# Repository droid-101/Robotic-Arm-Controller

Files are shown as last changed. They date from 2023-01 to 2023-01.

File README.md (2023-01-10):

# Robotic Arm Controller

## Background

### Pulse Width Modulation (PWM)

Pule Width Modulation is a a technique of sending variable electrical signals by using digital pulses. By turning a digital output on and off at varying frequencies, an effect can be produced where the signal is recieved at a fraction of the power. For example, a digital signal which is switched between an on state and an off state in equal intervals (50% of the time) will appear to be on at half power. Using this technique of altering the frequencies of these square pulses which are digital signals, variable electrical signals can be created using digital outputs. The servo motors on the robotic arm utilize PWM signals to operate. The PWM wires consist of three different wires carrying 5V+, signal, and GND respectively.

## Robotic Arm

The robotic arm has four different degrees of freedom, each controlled by a small servo motor. These four motors control rotation on the base, extension of the arm, the height of the claws, and the opening and closing of the claws. Each servo motor has a PWM cable over which it can recieve signals from the controller.

Robotic Arm

## Controller

The controller is a custom made Printed Circuit Board (PCB) which interfaces with the robotic arm's servo motors. It is designed to be plugged into a breadboard and connect to both an external microprocessor, and the robotic arm.

### Power Supply

The controller recieves power through a barrel jack. A 9V adapter is used to plug into a 120V wall socket and supplies the board with power through the barrel jack. Most of the electronic components on the board, as well as the servo motors on the arm, run on 5V. To downstep the voltage, three 7805 voltage regulators are used in parallel to both supply 5V to the circuit, and to prevent the board from overheating from high current draw.

### Controls

The controller has four potentiometers and one button as a part of its control set. Each potentiometer is isolated on its own channel on which it can be sampled for its current value by an external microprocessor. This allows for each joint on the robotic arm to have its own separate control. The button on the circuit board can also be read for its current state. It can serve as a trigger, or as a reset button.

### Reading and Writing

The controller has multiple sets of sip pins which connect to different components. The row of five sip pins connect to the button and potentionmeters and serve as inputs for the microprocessor to sample. The row of four sip pins are output pins which the microprocessor can use to write PWM signals to the servo motors. Each pin corresponds to a specific servo motor on the arm. The last set of four rows of three sip pins are connectors for the servo motors and allow for each motor to recieve power, and its respective signal from the microprocessor.

### Schematic
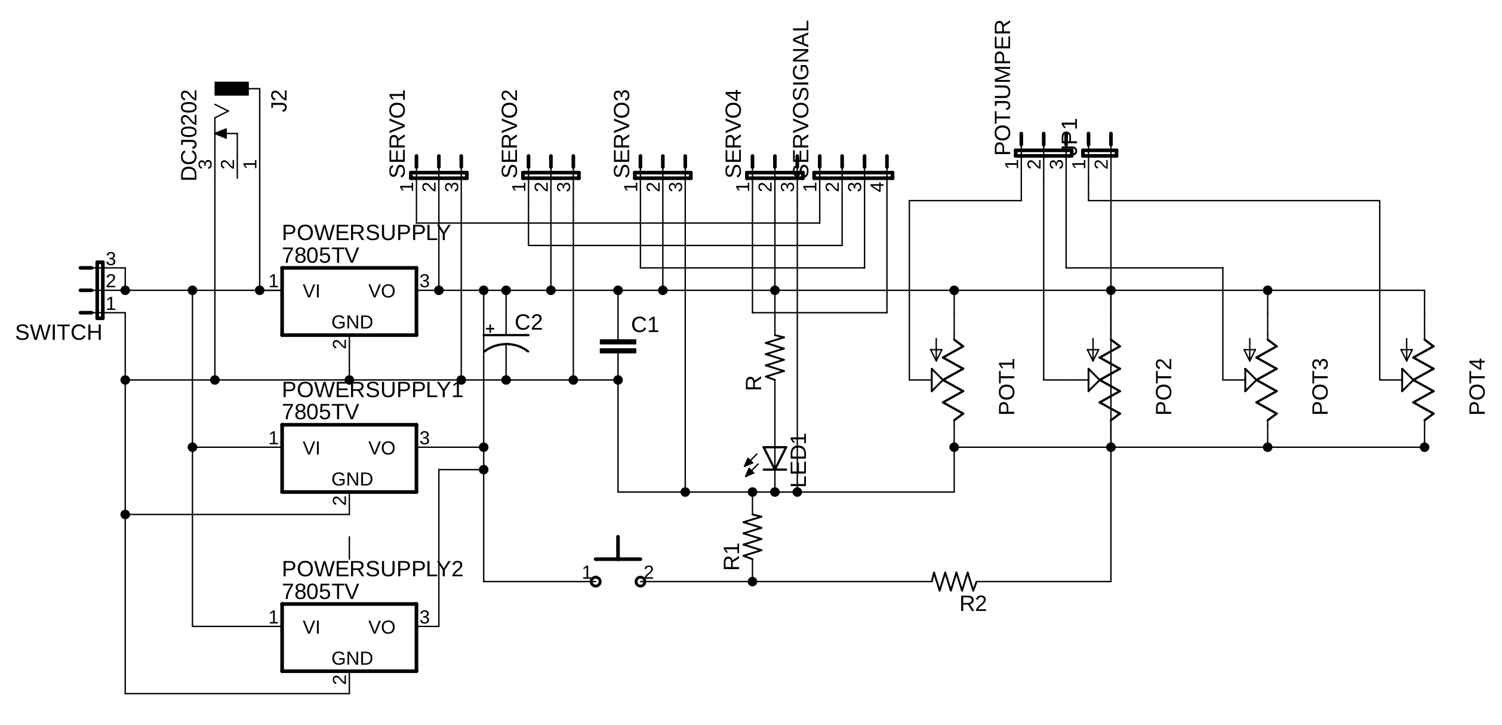
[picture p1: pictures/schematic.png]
Schematic


### Trace Mask
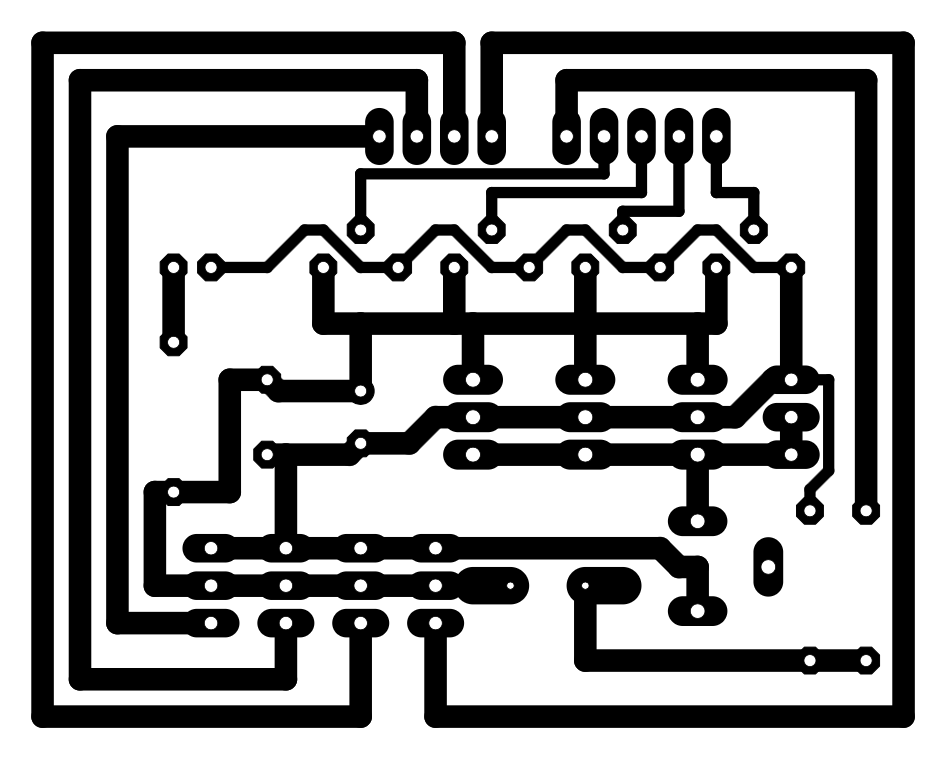
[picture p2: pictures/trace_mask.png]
Trace Mask


### Controller Circuit Board
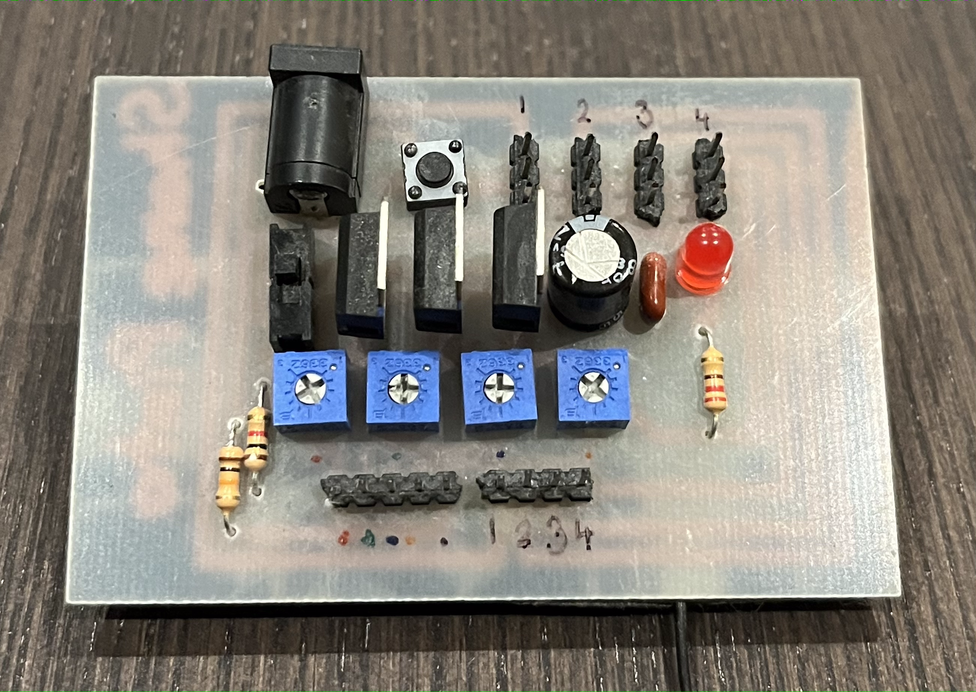
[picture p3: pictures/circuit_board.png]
Controller Circuit Board


## Arduino

The controller board was connected to an Arduino to manage reading the controls and writing angle values to the arm's servo motors. 

### Pinouts

The Arduino is capable of reading inputted analog signals which are inputted on the analog pins. Each potentiometer on the controller board is connected to one analog pin. The programme running on the Arduino will read the analog value on the pin and use it to write an angle to the servo motor. The Arduino has multiple digital pinouts which support PWM communication. These pins were used to send PWM signals to the servo motors. They output directly onto the signal lines feeding into the servo motors. Each pinout attaches to only one signal line and controls only one motor. The button on the controller board is also attached to one digital pin so that its state can be sampled.

### Keyboard Control

In addition to being controlled via the potentiometers on the circuit board, the robotic arm can also be controlled by a computer keyboard. Once the Arduino is connected to a computer using a USB cable, keyboard inputs are sent to the Arduino over Serial communication. The programme then determines which changes must be made to which motors depending on which key was pressed.

## Revisions

 After the PCB for the controller was created, a short circuit was found to exist in the printed traces. This was manually corrected on the underside of the board. Upon using the controller with the Arduino and the robotic arm, the servo motors were found to perform in a choppy fashion. This was solved by connecting the Arduino, the controller, and the servo motors to a common ground.

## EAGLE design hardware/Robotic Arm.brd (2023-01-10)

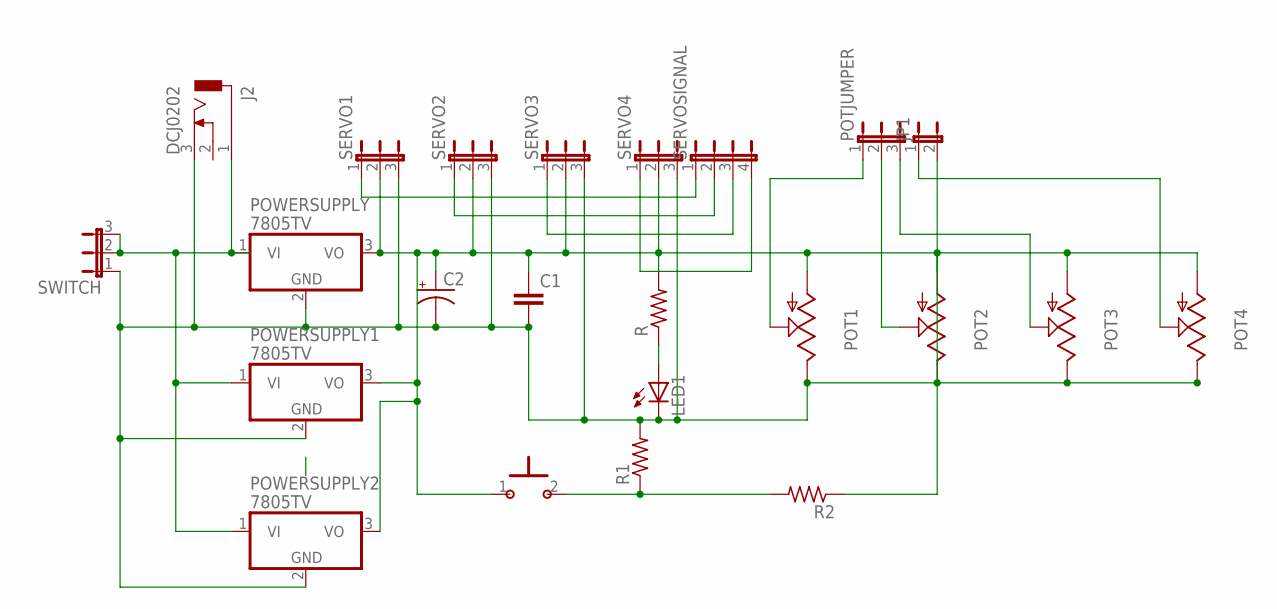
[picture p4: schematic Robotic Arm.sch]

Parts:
C1: C-EU050-025X075; C050-025X075
C2: CPOL-USE3.5-8; E3,5-8
J2: DCJ0202
JP1: JP1E; JP1
LED1: LED5MM
POT1, POT2, POT3, POT4: TRIM_US-B25P; B25P
POTJUMPER: JP2E; JP2
POWERSUPPLY, POWERSUPPLY1, POWERSUPPLY2: 7805TV; TO220V
R, R1, R2: R-US_0207/10; 0207/10
SERVO1, SERVO2, SERVO3, SERVO4: JP2E; JP2
SERVOSIGNAL: JP4E; JP4
SWITCH: JP2E; JP2
U$1: PUSHBUTTON

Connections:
unnamed: C1.2, C2.-, J2.3, LED1.K (C), POT1.E, POT2.E, POT3.E, POT4.E, POWERSUPPLY.2 (GND), POWERSUPPLY1.2 (GND), POWERSUPPLY2.2 (GND), R1.2, SERVO1.3, SERVO2.3, SERVO3.3, SERVO4.3, SWITCH.1
unnamed: C1.1, C2.+, POT1.A, POT2.A, POT3.A, POT4.A, POWERSUPPLY.3 (VO), POWERSUPPLY1.3 (VO), POWERSUPPLY2.3 (VO), R.2, SERVO1.2, SERVO2.2, SERVO3.2, SERVO4.2, U$1.1
unnamed: LED1.A, R.1
unnamed: J2.1, POWERSUPPLY.1 (VI), POWERSUPPLY1.1 (VI), POWERSUPPLY2.1 (VI), SWITCH.2, SWITCH.3
unnamed: POT1.S, POTJUMPER.1
unnamed: POT2.S, POTJUMPER.2
unnamed: JP1.1, POT4.S
unnamed: SERVO1.1, SERVOSIGNAL.1
unnamed: SERVO2.1, SERVOSIGNAL.2
unnamed: SERVO3.1, SERVOSIGNAL.3
unnamed: SERVO4.1, SERVOSIGNAL.4
unnamed: POT3.S, POTJUMPER.3
unnamed: R1.1, R2.2, U$1.2
unnamed: JP1.2, R2.1

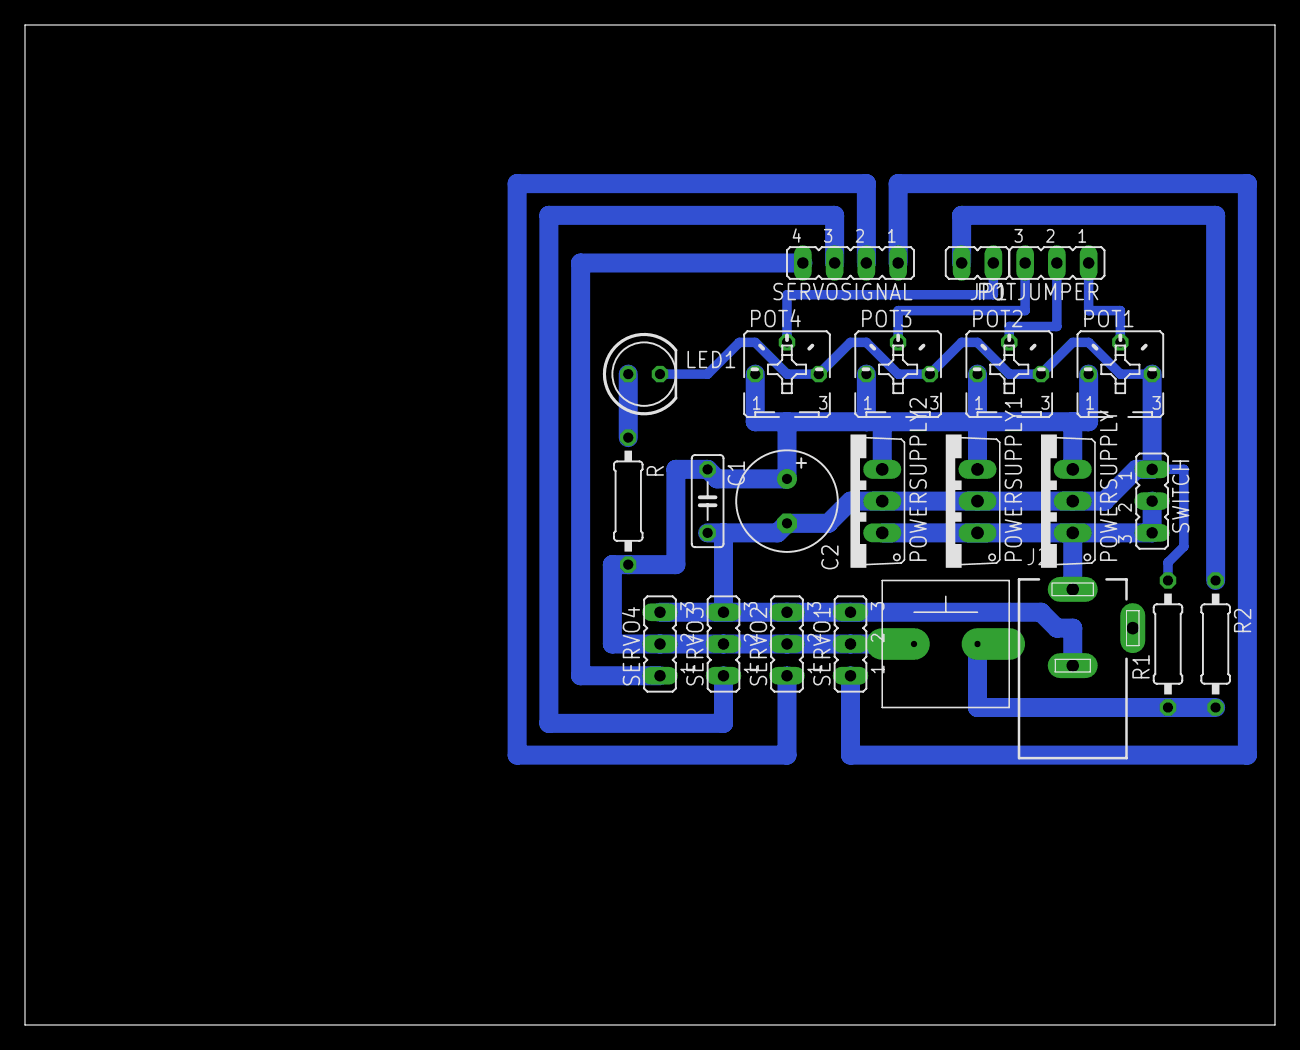
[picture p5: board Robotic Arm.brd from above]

Board: 2 copper layers, 100.0 x 80.0 mm, 23 parts (0 on the bottom side), 14 nets.

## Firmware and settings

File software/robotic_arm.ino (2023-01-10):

#include <Servo.h>

Servo myServo1;
Servo myServo2;
Servo myServo3;

int const potPin1 = A0;
int angle1;
int potVal1;

int const potPin2 = A1;
int angle2;
int potVal2;

int const potPin3 = A2;
int angle3;
int potVal3;

void setup()
{
 myServo1.attach(9); 
 myServo2.attach(10); 
 myServo3.attach(11); 
}

void loop()
{
 potVal1 = analogRead(potPin1);
 potVal2 = analogRead(potPin2);
 potVal3 = analogRead(potPin3);
 
 angle1 = potVal1/(1023/180);
 angle2 = potVal2/(1023/180);
 angle3 = potVal3/(1023/180);
 
 myServo1.write(angle1);
 delay(15);
 
 myServo2.write(angle2);
 delay(15);
 
 myServo3.write(angle3 + 90);
 delay(15);
}

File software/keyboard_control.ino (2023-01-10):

#include <Servo.h>

#define BASE_PIN       3
#define REACH_PIN      9
#define VERTICAL_PIN   10
#define CLAW_PIN       11

#define DEFAULT_BASE_POSITION      80.25
#define DEFAULT_REACH_POSITION     85
#define DEFAULT_VERTICAL_POSITION  120
#define DEFAULT_CLAW_POSITION      47

#define BASE_MIN      30
#define REACH_MIN     60
#define VERTICAL_MIN  80
#define CLAW_MIN      47

#define BASE_MAX      90
#define REACH_MAX     175
#define VERTICAL_MAX  175
#define CLAW_MAX      105

char key;

double baseAngle;
double reachAngle;
double verticalAngle;
double clawAngle;

Servo base;
Servo reach;
Servo vertical;
Servo claw;

void defaultPositions()
{
  base.write(DEFAULT_BASE_POSITION);
  delay(1000);
  reach.write(DEFAULT_REACH_POSITION);
  delay(1000);
  vertical.write(DEFAULT_VERTICAL_POSITION);
  delay(1000);
  claw.write(DEFAULT_CLAW_POSITION);
  delay(1000);
}



void setup()
{
  base.attach(BASE_PIN);
  reach.attach(REACH_PIN);
  vertical.attach(VERTICAL_PIN);
  claw.attach(CLAW_PIN);
  defaultPositions();

  baseAngle = DEFAULT_BASE_POSITION;
  reachAngle = DEFAULT_REACH_POSITION;
  verticalAngle = DEFAULT_VERTICAL_POSITION;
  clawAngle = DEFAULT_CLAW_POSITION;

  Serial.begin(115200);
}



void loop()
{
  
  if (Serial.available() > 0)
  {
    key = Serial.read();
    
    switch (key)
    {
      case 'd':
        if (baseAngle < BASE_MAX)
      {
        baseAngle += 1;
        base.write(baseAngle);
      }
        break;

      case 'a':
        if (baseAngle > BASE_MIN)
        {
        baseAngle -= 1;
        base.write(baseAngle);
        }
        break;
      
      case 'w':
        if (reachAngle < REACH_MAX)
        {
        reachAngle += 2;
        reach.write(reachAngle);
        }
        break;

      case 's':
        if (reachAngle > REACH_MIN)
        reachAngle -= 2;
        reach.write(reachAngle);
        break;

      case 'i':
        if (verticalAngle < VERTICAL_MAX)
        {
        verticalAngle += 2;
        vertical.write(verticalAngle);
        }
        break;

      case 'k':
        if (verticalAngle > VERTICAL_MIN)
        {
        verticalAngle -= 2;
        vertical.write(verticalAngle);
        }
        break;

      case 'l':
        if (clawAngle < CLAW_MAX)
        {
          clawAngle += 2;
          claw.write(clawAngle);
        }
        break;
      case 'j':
        if (clawAngle > CLAW_MIN)
        {
          clawAngle -= 2;
          claw.write(clawAngle);  
        }
        break;
      default:
        // nothing
        break;
    }
  }
}
